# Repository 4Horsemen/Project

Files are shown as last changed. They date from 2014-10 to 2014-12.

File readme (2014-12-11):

----------12/01/14 - 12/07/14 T17 Weekly Update 7-----------
*Thomas and Brian soldered all components onto their PCBs
*Thomas and Brian verified their PCBs had no solder bridges
*Fabricated bamboo parts for our Useless Box
*Worked on finalizing code for the Useless Box
*Designed arm mechanism for our Useless Box

----------11/24/14 - 11/30/14 T17 Weekly Update 6-----------
*Turned in HW#6
*Finished purchasing all components for PCB
*Thomas and Brian got cleared to work in the EPL & use
 the laser cutter, reflow oven, and soldering stations

----------11/17/14 - 11/23/14 T17 Weekly Update 5-----------
*Assembled our first board and baked it in the oven
*Started on HW#6
*Finalized the design for our test plan and test cases for HW#6

-----------11/10/14 - 11/16/14 T17 Weekly Update 4----------
Completed Tasks:
*Received our PCBs from Osh Park Manufacturing
*Began HW#5
*Researched HW#5
*Completed HW#5 Version #1
*Completed HW#5 Revision #2

-----------11/03/14 - 11/09/14 T17 Weekly Update 3-----------
Completed Tasks:
*Eliminated all unnecessary components in our PCB design
*Finalized our PCB design
*Submitted our PCB design inside the allotted time window
*Began HW#4
*Revised and expanded HW#4
*Completed HW#4
*Began to program Arduino and motor microcontrollers
*Ordered final parts

-----------10/27/14 - 11/02/14 T17 Weekly Update 2------------
Completed tasks:
*Got all of our ICs for our projects ordered
*Designed our schematic
*Fixed communication issues
*Finalized our black box
*Turned in HW#3 Rev#3
*Collective mentality shift.

-----------10/23/14 - 10/24/14 T17 Weekly Update 1------------
Completed tasks:
*Create a weekly update template
*Completed Rev1 HW 3
*Rough draft of Black box design completed

*Updated Block Diagram

To be done next week:
*Start ordering parts
*finish Atmega328 research
*finish LED Array research
*finish Servo research

Issues:
*Not sure what circuitry would be needed for LED arrays
*Not sure of motor/servo control circutry
*Getting Patrick, Ahmad, and Thomas on to git
*Getting the Atmega to respond to our preferences

---------------------------------------------------

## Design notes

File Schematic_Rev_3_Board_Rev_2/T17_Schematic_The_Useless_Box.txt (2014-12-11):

Partlist exported from C:/Users/Brian/Documents/GitHub/tut/Schematic_Rev_3_Board_Rev_2/T17_Schematic_The_Useless_Box.sch at 12/11/2014 2:39:47 PM

Part            Value                 Device                Package            Description                                 PROD_ID    TP_SIGNAL_NAME VALUE     
9V-BATTERY-CLIP M02LOCK               M02LOCK               1X02_LOCK          Standard 2-pin 0.1" header. Use with                                            
C1              10uF                  C-EUC0805             C0805              CAPACITOR, European symbol                                                      
C2              10uF                  C-EUC0805             C0805              CAPACITOR, European symbol                                                      
C3              10nF                  C-EUC0805             C0805              CAPACITOR, European symbol                                                      
C4              10nF                  C-EUC0805             C0805              CAPACITOR, European symbol                                                      
C5              10nF                  C-EUC0805             C0805              CAPACITOR, European symbol                                                      
C6              10uF                  C-EUC0805             C0805              CAPACITOR, European symbol                                                      
C7              10uF                  C-EUC0805             C0805              CAPACITOR, European symbol                                                      
C8              10nF                  C-EUC0805             C0805              CAPACITOR, European symbol                                                      
C9              10nF                  C-EUC0805             C0805              CAPACITOR, European symbol                                                      
C10             22pF                  C-EUC0805             C0805              CAPACITOR, European symbol                                                      
C11             22pF                  C-EUC0805             C0805              CAPACITOR, European symbol                                                      
C12             10nF                  C-EUC0805             C0805              CAPACITOR, European symbol                                                      
IC1                                   V_REG_78XX-TO-220     TO-220-ALT         Voltage Regulator                                                               
J1              AVR_SPI_PRG_6NS       AVR_SPI_PRG_6NS       2X3-NS             AVR ISP 6 Pin                                                                   
JP3             ARM_SERVO             M03PTH                1X03               Header 3                                                                        
JP4             LID_SERVO             M03PTH                1X03               Header 3                                                                        
L-MOTOR         M02LOCK               M02LOCK               1X02_LOCK          Standard 2-pin 0.1" header. Use with                                            
PROGRAMMING                           M06NO_SILK_FEMALE_PTH 1X06_NO_SILK       Header 6                                    CONN-08437                          
Q1              16MHz                 XTAL/S                QS                 CRYSTAL                                                                         
R-MOTOR         M02LOCK               M02LOCK               1X02_LOCK          Standard 2-pin 0.1" header. Use with                                            
R1              0                     R-EU_R0805            R0805              RESISTOR, European symbol                                                       
R2              10K                   R-EU_R0805            R0805              RESISTOR, European symbol                                                       
R3              10K                   R-EU_R0805            R0805              RESISTOR, European symbol                                                       
R4              10K                   R-EU_R0805            R0805              RESISTOR, European symbol                                                       
R5              10K                   R-EU_R0805            R0805              RESISTOR, European symbol                                                       
R6              10K                   R-EU_R0805            R0805              RESISTOR, European symbol                                                       
S1              SWITCH-MOMENTARY-2SMD SWITCH-MOMENTARY-2SMD TACTILE-SWITCH-SMD Various NO switches- pushbuttons, reed, etc SWCH-08247                          
TOGGLE          M02LOCK               M02LOCK               1X02_LOCK          Standard 2-pin 0.1" header. Use with                                            
U$1             LB1938FA-AH           LB1938FA-AH           MSOP8                                                                                              
U$2             LB1938FA-AH           LB1938FA-AH           MSOP8                                                                                              
U1              ATMEGA328P            ATMEGA328_SMT         TQFP32-08          32-Pin Atmega328 part                       IC-09069                  ATMEGA328P

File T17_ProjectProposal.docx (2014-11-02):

HW #2: Project Proposal

Useless Box!!

The design is a simplistic 3.5"x4.5"x3.5" box with a switch on the lid.

Must

- Have a box
- Have a switch
- Have a servo
- Have a battery

Can

- Have a second, hidden, switch for power turning the lid switch into a signal
- Have Motors and hidden wheels to create an interactive experience
- Have a second servo to make movements more distinct (one lifts lid, second flips switch)
- Have a Gyroscope to sense direction and speed for greater control on interaction.
- Have a proximity sensor to stay on the table

May

- Add LED/LCD/OLED display programmed to express emotion

The box itself will listen for or be powered by a switch on the lid, which will cause a compartment on the lid to lift, and allow a servo controlled "finger" to be revealed and flip the switch back to the original position for an indefinite number of times. The project can have it's difficulty scaled up from there to include extra sensors, servos, and motors for a more complex movement and interaction experienced by the operator. It also may have peripherals such as LED displays to create a character out of the box and give it emotion.

ECE 411 Fall 2014 practicum project wiki Authors: Patrick L., Ahmad Q., Thomas S. Brian A.

| difficulty | programming difficulty | circuitry | Mechanical difficulty | research | Scalability | cost | | scale
rudder pedals | 6 | 7.5 | 6 | 7 | 3 | 1 | 5 | | 1. so simple a child can do it
transformer soft start | 8 | 3 | 8 | 5 | 10 | 3 | 10 | | 5. Easily doable by a EE Jr.
transcranial mag ther | 10 | 10 | 10 | 6 | 10 | 10 | 10 | | 10. Research level engineering
mobile charge det. | 7 | 5 | 8 | 5 | 6 | 1 | 5
slot cars | 7.5 | 3 | 8 | 8 | 4 | 1 | 7
useless box | 5 | 3 | 3 | 6.5 | 3 | 1 | 4
critera priority: (rated highest to lowest) | 7 | 3 | 2 | 1 | 4 | 6 | 5

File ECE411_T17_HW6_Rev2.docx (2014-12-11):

Ahmad Qazi

Brian Andrews (T17)

Patrick Liggett

Thomas Scarpinatto

November 24, 2014

# ECE411 HW # 6: Test Plan Rev 2

## Comprehensive Hierarchical Test Plan

THE USELESS BOX: System Test Plan

1. INTRODUCTION
  1.1 This Document
  1.2 Conduct System Tests
2. REFERENCE DOCUMENTS
  2.1 Design Documentation

• TBU Requirements Document, Rev 3

• TBU Project Schedule, Rev 2

• TBU System Design/Modeling, Rev 2

• TBU Block Level Diagram, Rev 3

• TBU Power Supply Schematic, Rev 2

• TBU Comprehensive Schematic, Rev 3.5

• TBU Board Layout, Rev 3

  2.2 Other

• Atmel ATMega328 Design Specifications

• Atmel ATMega328 8-Bit Microcontroller Datasheet

• ON Semiconductor LB1938FA Motor Driver Datasheet

3. TBU Overview
  3.1 Operational Description
  3.2 Definition of Terminology
4. PRETEST PREPARATION
  4.1 Test Equipment

• Tektronix Multimeter DMM4020

4.2 Test Setup and Calibration

5. The Switch
  5.1 Verify Switch is Active High
  5.2 Verify Switch is the only input
  5.3 Switch fires high every time it is thrown on
6. ATMega328
  6.1 Verify signal input each time switch is toggled to high position
  6.2 Verify that servos get signal each time the switch is toggled
  6.3 Verify that Motor Control Chip (MCC) gets sent a signal every eighth time the switch is toggled
7. Motor Control Chip (MCC)
  7.1 Verify that MCC receives signal every eighth time the switch is toggled
  7.2 Verify sequence of forward and reverse on wheel motors
8. Power Supply
  8.1 Verify 5V output
  8.2 Verify input and output current within supply specifications

## Test Case # 1: The Toggle Switch

Test Writers: Ahmad Qazi, Brian Andrews, Patrick Liggett, Thomas Scarpinatto
Test Case Name: | | The Useless Box Test #1 | | | | Test ID #: | | TUB-01
Description: | | Verify that the toggle switch is the only input signal for the whole system. | | | | Type: | | Black box

Tester Information
| Name of Tester: | | | | | | Date:
Hardware Ver: | | 1.0 | | | | | Time:
Setup: | | Make sure the Switch is in off position and the battery is viable.
Step | Action | Expected Result | Pass | Fail | N/A | | Comments
1 | Plug lead into test point between switch and ATMega328 | Test lead should fit into point
2 | Verify zero signal before engaging switch | Meter should read zero signal
3 | Flip switch to on position | Meter should read 5V
4 | Record data gathered | Meter readings should be within design parameters
Overall Test Result:

## Test Case # 2: ATMega328

Test Writers: Ahmad Qazi, Brian Andrews, Patrick Liggett, Thomas Scarpinatto
Test Case Name: | | The Useless Box Test #2 | | | | Test ID #: | | TUB-02
Description: | | | | | | Type: | | Black box

Tester Information
| Name of Tester: | | | | | | Date:
Hardware Ver: | | 1.0 | | | | | Time:
Setup: | | Plug leads in test points between switch and ATMega328, between ATMega328 and Arm Servo, between ATMega328 and Lid Servo and between ATMega328 and Motor Control Chip.
Step | Action | Expected Result | Pass | Fail | N/A | | Comments
1 | Plug lead into test point between switch and ATMega328 | Signal should be zero when switch is low and 5V when switch is high.
2 | Plug lead into test point between ATMega328 and Arm Servo | Signal through Arm servo should be zero when switch is low and 5V when switch is high.
3 | Plug lead into test point between ATMega328 and Lid Servo | Signal through Lid servo should be zero when switch is low and 5V when switch is high.
4 | Plug lead into test point between ATMega328 and Motor Control Chip | Signal through MCC should be zero when switch is low and 5V when switch is high.
Overall Test Result:

## Test Case # 3: Motor Control Chip

Test Writers: Ahmad Qazi, Brian Andrews, Patrick Liggett, Thomas Scarpinatto
Test Case Name: | | The Useless Box Test #3 | | | | Test ID #: | | TUB-03
Description: | | Check if Motor Control Chip (MCC) activates when triggered and functions correctly | | | | Type: | | Black box

Tester Information
| Name of Tester: | | | | | | Date:
Hardware Ver: | | 1.0 | | | | | Time:
Setup: | | Make proper connections to the MCC daughterboard via ATMega328 or Arduino.
Step | Action | Expected Result | Pass | Fail | N/A | | Comments
1 | Toggle switch every 8th time to verify that MCC activates | TBU moves due to activation.
2 | Truth table (TT) verification by using given truth table | Truth table outputs match given TT.
Overall Test Result:

## Test Case # 4: Power Supply

Test Writers: Ahmad Qazi, Brian Andrews, Patrick Liggett, Thomas Scarpinatto
Test Case Name: | | The Useless Box Test #4 | | | | Test ID #: | | TUB-04
Description: | | System should run on a 9V battery but converts to 5V during the process | | | | Type: | | Black box

Tester Information
| Name of Tester: | | | | | | Date:
Hardware Ver: | | 1.0 | | | | | Time:
Setup: | | Connect 9V battery to IC
Step | Action | Expected Result | Pass | Fail | N/A | | Comments
1 | Verify output voltage is 5V | Output is found to be 5V
2 | Measure I/O current and check if it is within supply specifications | I/O current is found to be ≤ 1.5 A
Overall Test Result:

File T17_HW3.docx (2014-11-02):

ECE411: Industry Design Processes: HW # 3

Brian Andrews, Ahmad Qazi, Patrick Liggett, Thomas Scarpinatto

Oct 27, 2014

REV 3

Must

• Have a box

• Have a switch

• Have a servo

• Have a battery

Can

• Have a second, hidden, switch for power turning the lid switch into a signal

• Have Motors and hidden wheels to create an interactive experience

• Have a second servo to make movements more distinct (one lifts lid, second flips switch)

• Have a Gyroscope to sense direction and speed for greater control on interaction.

• Have a proximity sensor to stay on the table

May

• Add LED/LCD/OLED display programmed to express emotion

Marketing Requirements | Engineering Requirements | Justification
2-4 | 1. System should run on a 9V Battery | Increases the runtime of the device, and keeps the device portable.
2, 3 | 2. The box dimensions should not exceed 6”x5”x3” | The small size keeps the product portable. This means it can be used as a small entertainment device such as a "Newton's cradle" or "infinite slinky"
1, 2 | 3. Microcontroller should have a minimum of 1 PWM. Should have a minimum of 10 programmable I/O lines. Maximum of 9V. Minimum of 512 bytes of internal SRAM. Should be operated at milspec temperatures. | Ensures that the useless box can operate at room temperature, low power, and still run the necessary components.
1, 2 | 4. Should have one motorized arm, one moveable door, and two switches. | The low number of actuators and inputs reduces the overall cost and complexity of the design.
2 | 5. Production cost should not exceed $40. | This is based on competitive market and the non-commercialized nature of the device.

Marketing Requirements

1. The system should be robust enough to withstand being dropped repeatedly as well as being water resistant. The switches must not break and be able to withstand constant use.
2. The system should be low cost for ease of Marketing.
3. The system should be portable. The device should be able to fit into a backpack pocket or briefcase compartment.

4. The system should be easy to use. The device will have at most two

switches.

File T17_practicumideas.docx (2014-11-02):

Ahmad Qazi

Brian Andrews

Patrick Liggett

Thomas Scarpinatto

Oct 13, 2014

ECE411: INDUSTRY DESIGN PROCESSES: PROJECT PROPOSAL

1) Rudder Pedals (for Simulator Use)- All planes have a flap on the tail that is used to help the plane turn left or right based upon the flap’s position. These are controlled by a pair of pedals in the cockpit that upon depressing the corresponding left or right pedal shifts the rudder into position for turning left/right. Many video games that involve plane flight simulate this rudder as a part of the game’s mechanics. While usually these are pre-programmed to react perfectly due to the limited number of inputs a player has access to.

Many people who play games that involve plane flight prefer to use a H.O.T.A.S. (Hands On Throttle And Stick) setup in order to have a more intimate and realistic experience. The downside of this setup is that you no longer have access to keyboard shortcuts that allow control of the plane’s rudder. Many of these H.O.T.A.S. setups solve this by making the flight stick have a rotational axis for rudder control, Some companies even offer highly priced pedal sets to appease the gamers who prefer a more realistic experience. The proposal is to design a microcontroller based system that could be easily self assembled and turned into rudder pedals that can be used in these simulation games.

2) Transformer Soft Start – When a transformer is first powered up, it can grab as much as forty times its rated operating current, causing very serious heat rise in the laminations of the core. Each time this happens, the lifespan of the transformer is reduced. In times past, this has been a very minor issue, but grid power becomes more and more distributed, especially with intermittent power supplies from renewable sources such as wind turbines and photovoltaics, transformers are being switched on and off more and more, thereby greatly increasing wear and tear and shortening the lifespan of the transformer.

Given that the purchase lead-time on a utility scale transformer is around three years, the need to maximize transformer lifetime is paramount. Additionally, many of the locations for renewable sources of power such as wind turbines and wave power generation sites are in very out-of-the-way locales that have no back-up transformers that can be paralleled in to maintain a continuous flow of power. What this translates to is that potentially hundreds of millions of dollars worth of power generating equipment sits idle while the transformer is either repaired in field or removed and replaced.

What we propose is a soft starting mechanism similar to that used by large DC motors, especially ones with large physical loads present on startup. A bank of resistors would be placed in-line for the start up of the transformer with a resistor being removed each time the transformer reaches a predetermined level of power so that the startup is much more gradual and thereby does not superheat the laminations inside the transformer core. Our device would monitor the flux increase inside the core and pull out resistors as the transformer meets predefined criteria, thereby increasing life expectancy and decreasing maintenance costs.

3) Transcranial Magnetic Therapy Device (TCrMT) – Transcranial Magnetic Therapy (TCrMT) has been a boon for bipolar, schizophrenic, and head trauma patients, but so far has been used mostly in a laboratory context. This valued treatment is not widely available to patients that desperately need it when it should be available everywhere. Our proposal is to make a small, portable TCrMT device that can be carried around in a backpack and is ready for deployment at a moment’s notice so that the patient does not have to live in fear of having an episode of seizures or a psychotic episode out in the general public. The patient would self-conduct the treatment by placing a special cap on their head and plugging it into the TCrMT device and pressing a single start button.

The length of the treatment would be determined by simple mechanical switches and push buttons that are ruggedized to withstand the inevitability of being dropped and tossed about. Power will come from a lithium-ion polymer battery that can be recharged from 120/240 VAC or 12 VDC power sources. This device would be mostly absent of sophisticated ICs to hold down device cost and to increase reliability and device longevity.

4) Mobile Charge Detection Device – Electricians have very simple detection devices that will tell you if a cable is energized or not, but what we put forward is a mobile device that detects not just power, but what type. Specifically, this device would be able to discern the difference between AC and DC power sources, and if the power detected is AC, then the components of real and reactive power would be displayed in their respective proportions on an easy to view lighted screen. Such a device would be very useful for diagnosis in large IC fabrication units and laboratory settings so that the safety and integrity of hypersensitive test equipment, some devices costing millions of dollars, is assured. We would also like the device, if it is so possible to achieve, to be able to see power conduits through sheet rock so that electricians and handymen do not injure themselves by accidentally striking hot power lines that they cannot see.

5) Slot Cars!! - The proposal here is to design a track and car base system. The tracks should be usable like a puzzle piece allowing players to design their own track as long as it contains the keystone track that has the controllers attached. This can be as simple as an oval for demonstration purposes. As for the cars, if we can design a base that allows tops to be clipped on we could make it so that the bodies of the cars themselves can be 3-D printable.

6) Useless Box!! - A box with a switch on top, as simple a design as could be. What happens when we flip the switch? A lid lifts away from the rest of the box and out pops a little finger shaped object that rotates up and flips the switch back. This can scale up in difficulty or down very easily, with extra time we can add to the software and hardware making the box react differently (back away from it’s original position, drive around, spin in place, make faces on LED arrays etc.)

According to the Decision Matrix attached

1. Useless Box
2. Mobile Charge Detection Device
3. Rudder Pedals
4. Slot Cars

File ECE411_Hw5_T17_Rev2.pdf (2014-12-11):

# ECE411: INDUSTRY DESIGN PROCESSES

# HOMEWORK 5

# REV 2

## BRIAN ANDREWS

## THOMAS SCARPINATTO

## AHMAD QAZI

## PATRICK LIGGETT

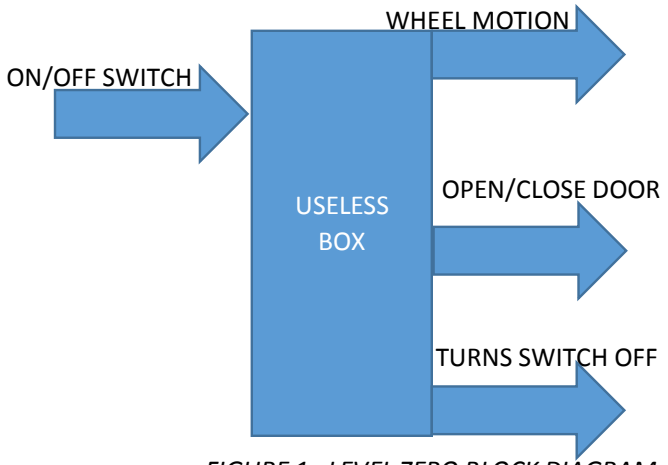
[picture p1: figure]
WHEEL MOTION; ON/OFF SWITCH; OPEN/CLOSE DOOR; TURNS SWITCH OFF; USELESS BOX

FIGURE 1: LEVEL ZERO BLOCK DIAGRAM

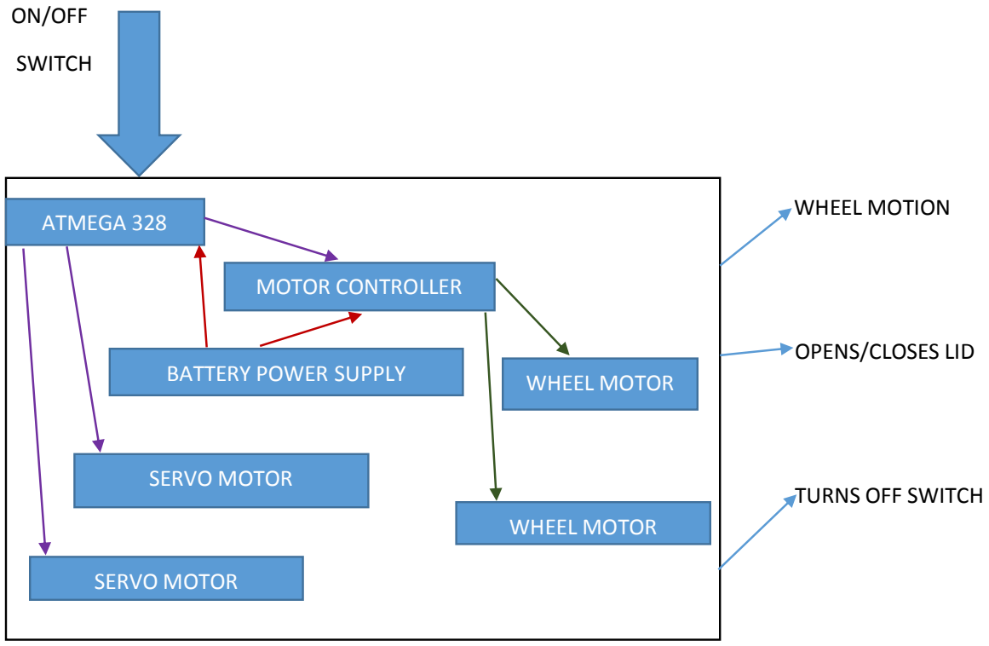
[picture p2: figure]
ON/OFF; SWITCH; WHEEL MOTION; OPENS/CLOSES LID; TURNS OFF SWITCH; ATMEGA 328; MOTOR CONTROLLER; BATTERY POWER SUPPLY; WHEEL MOTOR; SERVO MOTOR

FIGURE 2: LEVEL ONE BLOCK DIAGRAM

## LEVEL-0 DIAGRAM FOR EACH SUB-COMPONENT

SWITCH | ATMega328

User Input

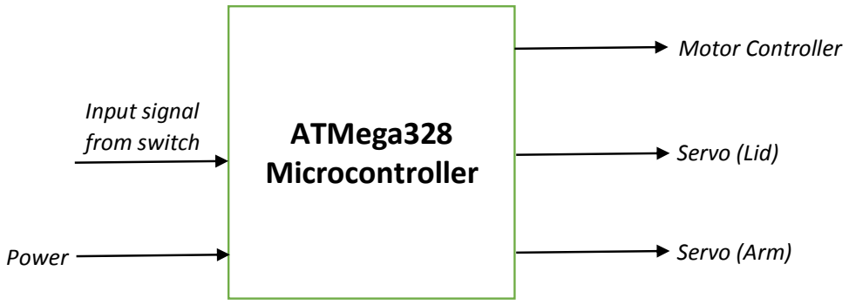
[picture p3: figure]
ATMega328 Microcontroller; Motor Controller; Servo (Lid); Servo (Arm); Input signal from switch; Power

### Motor Controller

# 1

Wheel Motor #1 ATMega328

Power

### Motor Controller

# 2

Wheel Motor #2 ATMega328

Power

Lid Servo | Lid ATMega328

Power

Arm Servo | Arm

Power

ATMega328

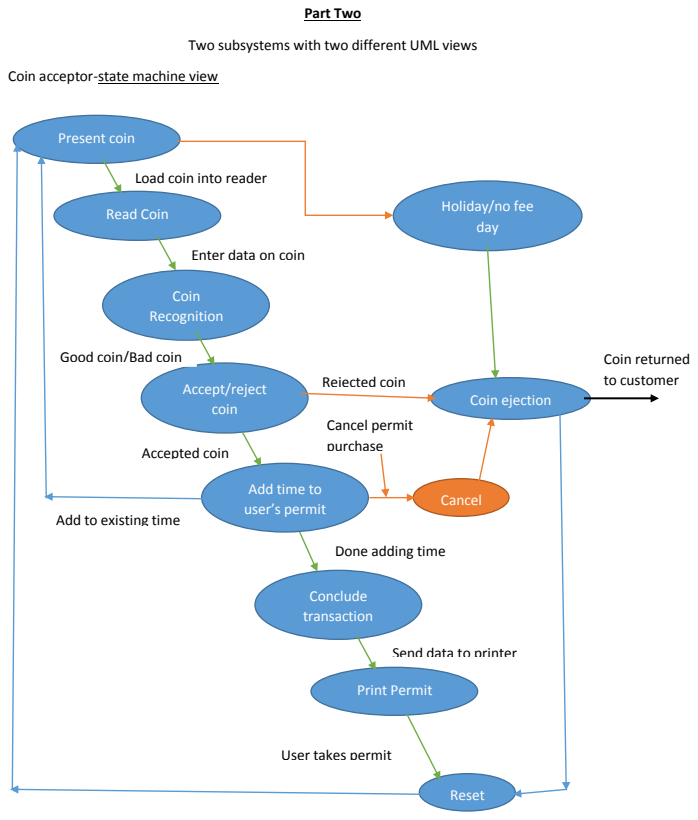
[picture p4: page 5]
Part Two; Present coin; Read Coin; Coin Recognition; Accept/reject coin; Conclude transaction; Print Permit; Reset; Cancel; Coin ejection; Rejected coin; Accepted coin; Cancel permit purchase; Coin returned to customer

Two subsystems with two different UML views

Coin acceptor-state machine view

Load coin into reader

Holiday/no fee
day

Enter data on coin

Good coin/Bad coin

Add time to
user’s permit

Add to existing time

Done adding time

Send data to printer

User takes permit

## THE COIN ACCEPTOR – PHYSICAL VIEW

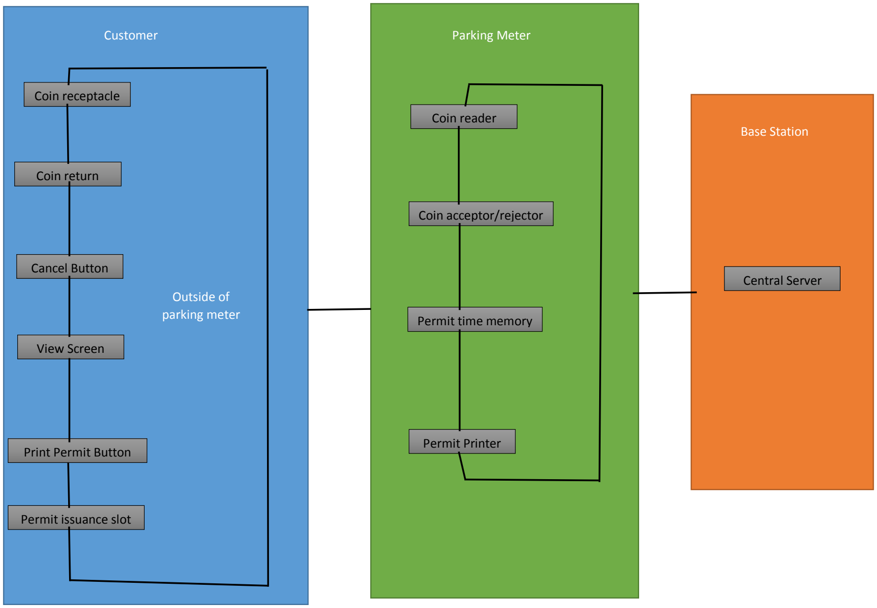
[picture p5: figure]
Customer; Coin receptacle; Coin return; Cancel Button; View Screen; Print Permit Button; Permit issuance slot; Outside of parking meter; Parking Meter; Coin reader; Coin acceptor/rejector; Permit time memory; Permit Printer; Base Station; Central Server

## THE CREDIT CARD READER – THE STATE MACHINE VIEW

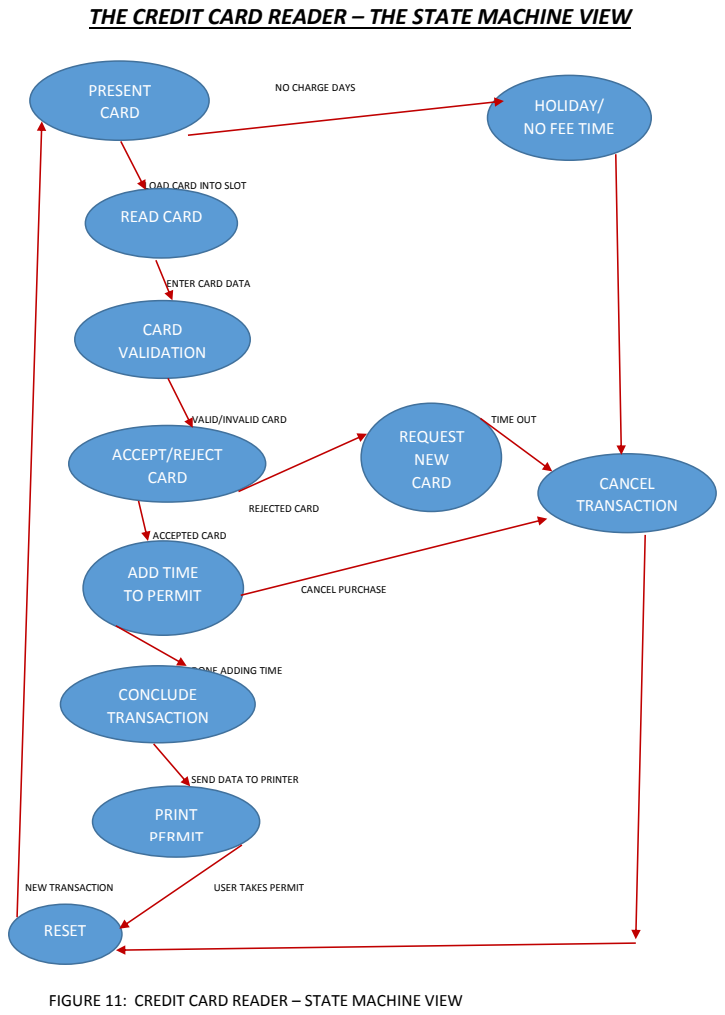
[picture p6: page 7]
VALID/INVALID CARD; TIME OUT; REJECTED CARD; ACCEPTED CARD; CANCEL PURCHASE; NEW TRANSACTION; USER TAKES PERMIT; PRESENT CARD; CARD VALIDATION; ACCEPT/REJECT CARD; ADD TIME TO PERMIT; CONCLUDE TRANSACTION; RESET; REQUEST NEW; CARD; CANCEL; TRANSACTION

NO CHARGE DAYS

HOLIDAY/
NO FEE TIME

LOAD CARD INTO SLOT
READ CARD

ENTER CARD DATA

DONE ADDING TIME

SEND DATA TO PRINTER
PRINT
PERMIT

FIGURE 11: CREDIT CARD READER – STATE MACHINE VIEW

# CREDIT READER – INTERACTION VIEW

Customer | Parking Meter | Base Station | CC Database

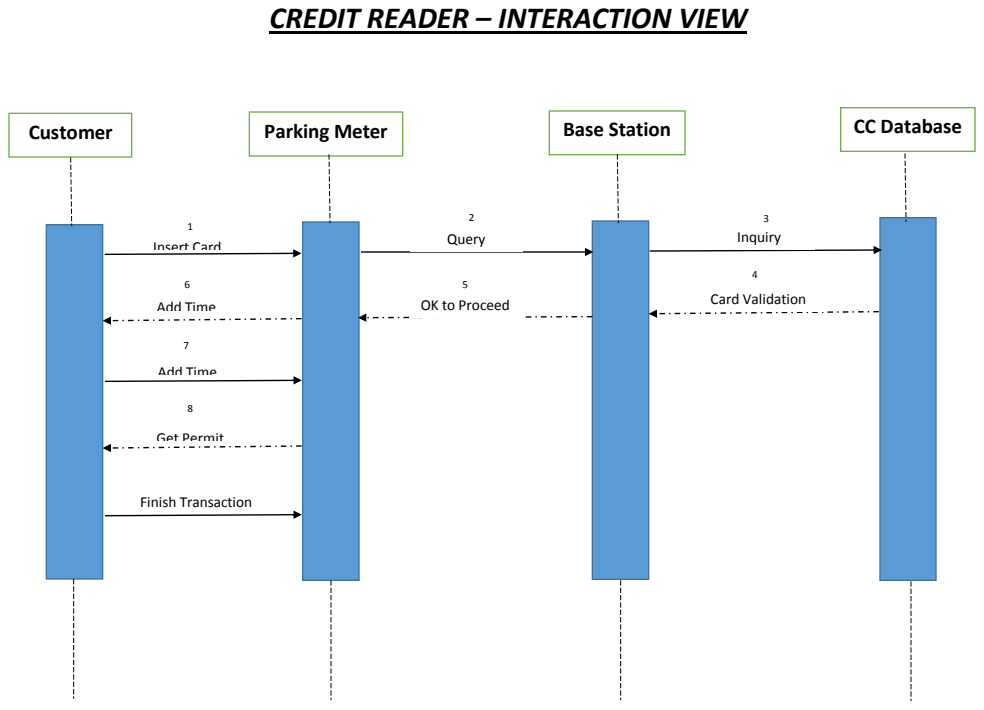
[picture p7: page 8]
Insert Card; Add Time; Get Permit; Finish Transaction; Query; Inquiry; Card Validation

OK to Proceed

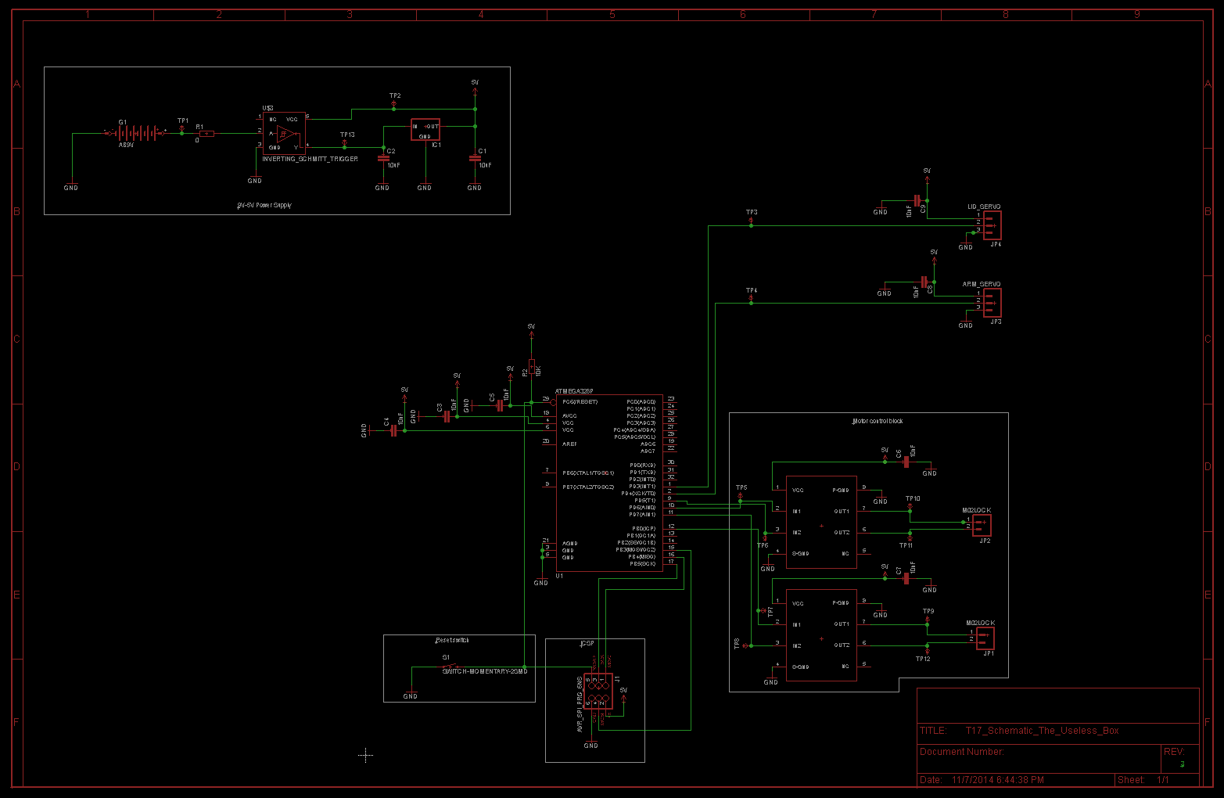
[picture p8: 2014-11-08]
T17_Schematic_Image.PNG

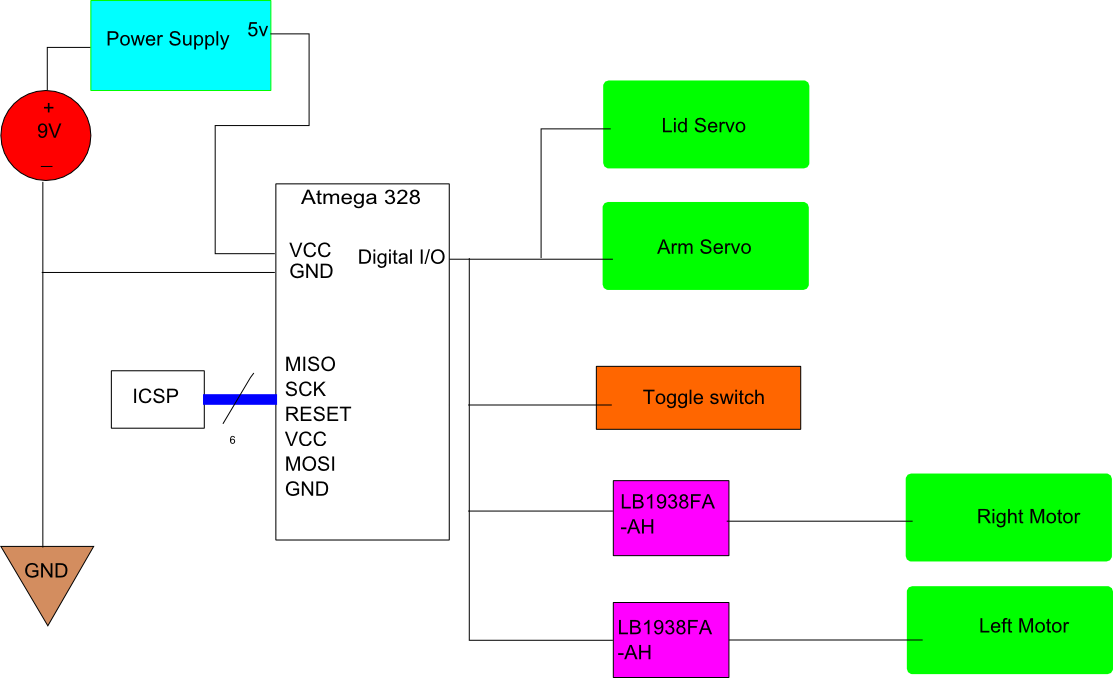
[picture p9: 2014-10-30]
T17_Blackbox.png

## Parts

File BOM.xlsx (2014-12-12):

PART | VALUE | DEVICE | PACKAGE | Description | Product ID | PRICE FOR 1 | PRICE FOR 1000
C1 | 10uF | C-EUC0805 | C0805 | CAPACITOR, European symbol |  | $0.17 | $31.63
C2 | 10uF | C-EUC0806 | C0806 | CAPACITOR, European symbol |  | $0.17 | $31.63
C3 | 10uF | C-EUC0807 | C0807 | CAPACITOR, European symbol |  | $0.17 | $31.63
C4 | 10uF | C-EUC0808 | C0808 | CAPACITOR, European symbol |  | $0.17 | $31.63
C5 | 10uF | C-EUC0809 | C0809 | CAPACITOR, European symbol |  | $0.17 | $31.63
C6 | 10uF | C-EUC0810 | C0810 | CAPACITOR, European symbol |  | $0.17 | $31.63
C7 | 10uF | C-EUC0811 | C0811 | CAPACITOR, European symbol |  | $0.17 | $31.63
C8 | 10uF | C-EUC0812 | C0812 | CAPACITOR, European symbol |  | $0.17 | $31.63
C9 | 10uF | C-EUC0813 | C0813 | CAPACITOR, European symbol |  | $0.17 | $31.63
C10 | 22pF | C-EUC0814 | C0814 | CAPACITOR, European symbol |  | $0.10 | $15.60
C11 | 22pF | C-EUC0815 | C0815 | CAPACITOR, European symbol |  | $0.10 | $15.60
C12 | 10nF | C-EUC0816 | C0816 | CAPACITOR, European symbol |  | $0.36 | $86.95
IC1 |  | V_REG_78XX-TO-220 | TO-220-ALT | Voltage Regulator |  | $4.30 | $3604.32
 |  |  |  | 40 pin header row |  | $0.56 | $282.15
JP3 | ARM_SERVO | M03PTH | 1X03 | Header 3 |  | $8.95 | $7160.00
JP4 | LID_SERVO | M03PTH | 1X03 | Header 3 |  | $8.95 | $7160.00
LMOTOR | M02LOCK | M02LOCK | 1X02_LOCK | Standard 2-pin 0.1" header. Use with |  | $0.50 | $500.00
RMOTOR | M02LOCK | M02LOCK | 1X02_LOCK | Standard 2-pin 0.1" header. Use with |  | $0.50 | $500.00
Q1 | 16MHz | XTAL/S | QS | CRYSTAL |  | $0.36 | $1.92
R1 | 0
R2 | 10K | R-EU_R0805 | R0805 | RESISTOR, European symbol |  | $0.10 | $7.04
R3 | 10K | R-EU_R0806 | R0806 | RESISTOR, European symbol |  | $0.10 | $7.04
R4 | 10K | R-EU_R0807 | R0807 | RESISTOR, European symbol |  | $0.10 | $7.04
R5 | 10K | R-EU_R0808 | R0808 | RESISTOR, European symbol |  | $0.10 | $7.04
R6 | 10K | R-EU_R0809 | R0809 | RESISTOR, European symbol |  | $0.10 | $7.04
S1 | SWITCH-MOMENTARY-2SMD | SWITCH-MOMENTARY-2SMD | TACTILE-SWITCH-SMD | Various NO switches- pushbuttons, reed, etc SWCH-08247
IC2 | LB1938FA-AH | LB1938FA-AH | MSOP8 |  |  | $1.63 | $759.90
IC3 | LB1938FA-AH | LB1938FA-AH | MSOP8 |  |  | $1.63 | $759.90
MICROPROCESSOR |  | ATMEGA 328P | 32TQFP | 32-Pin Atmega328 part |  | $7.40 | $3790.53
BATTERY CLIP | M02LOCK | M02LOCK | Standard 2-pin 0.1" header. Use with |  | IC-09069
TOGGLE |  |  |  |  |  | $4.32 | $2520.00
 |  |  |  |  | TOTAL | $41.69 | $27,476.74

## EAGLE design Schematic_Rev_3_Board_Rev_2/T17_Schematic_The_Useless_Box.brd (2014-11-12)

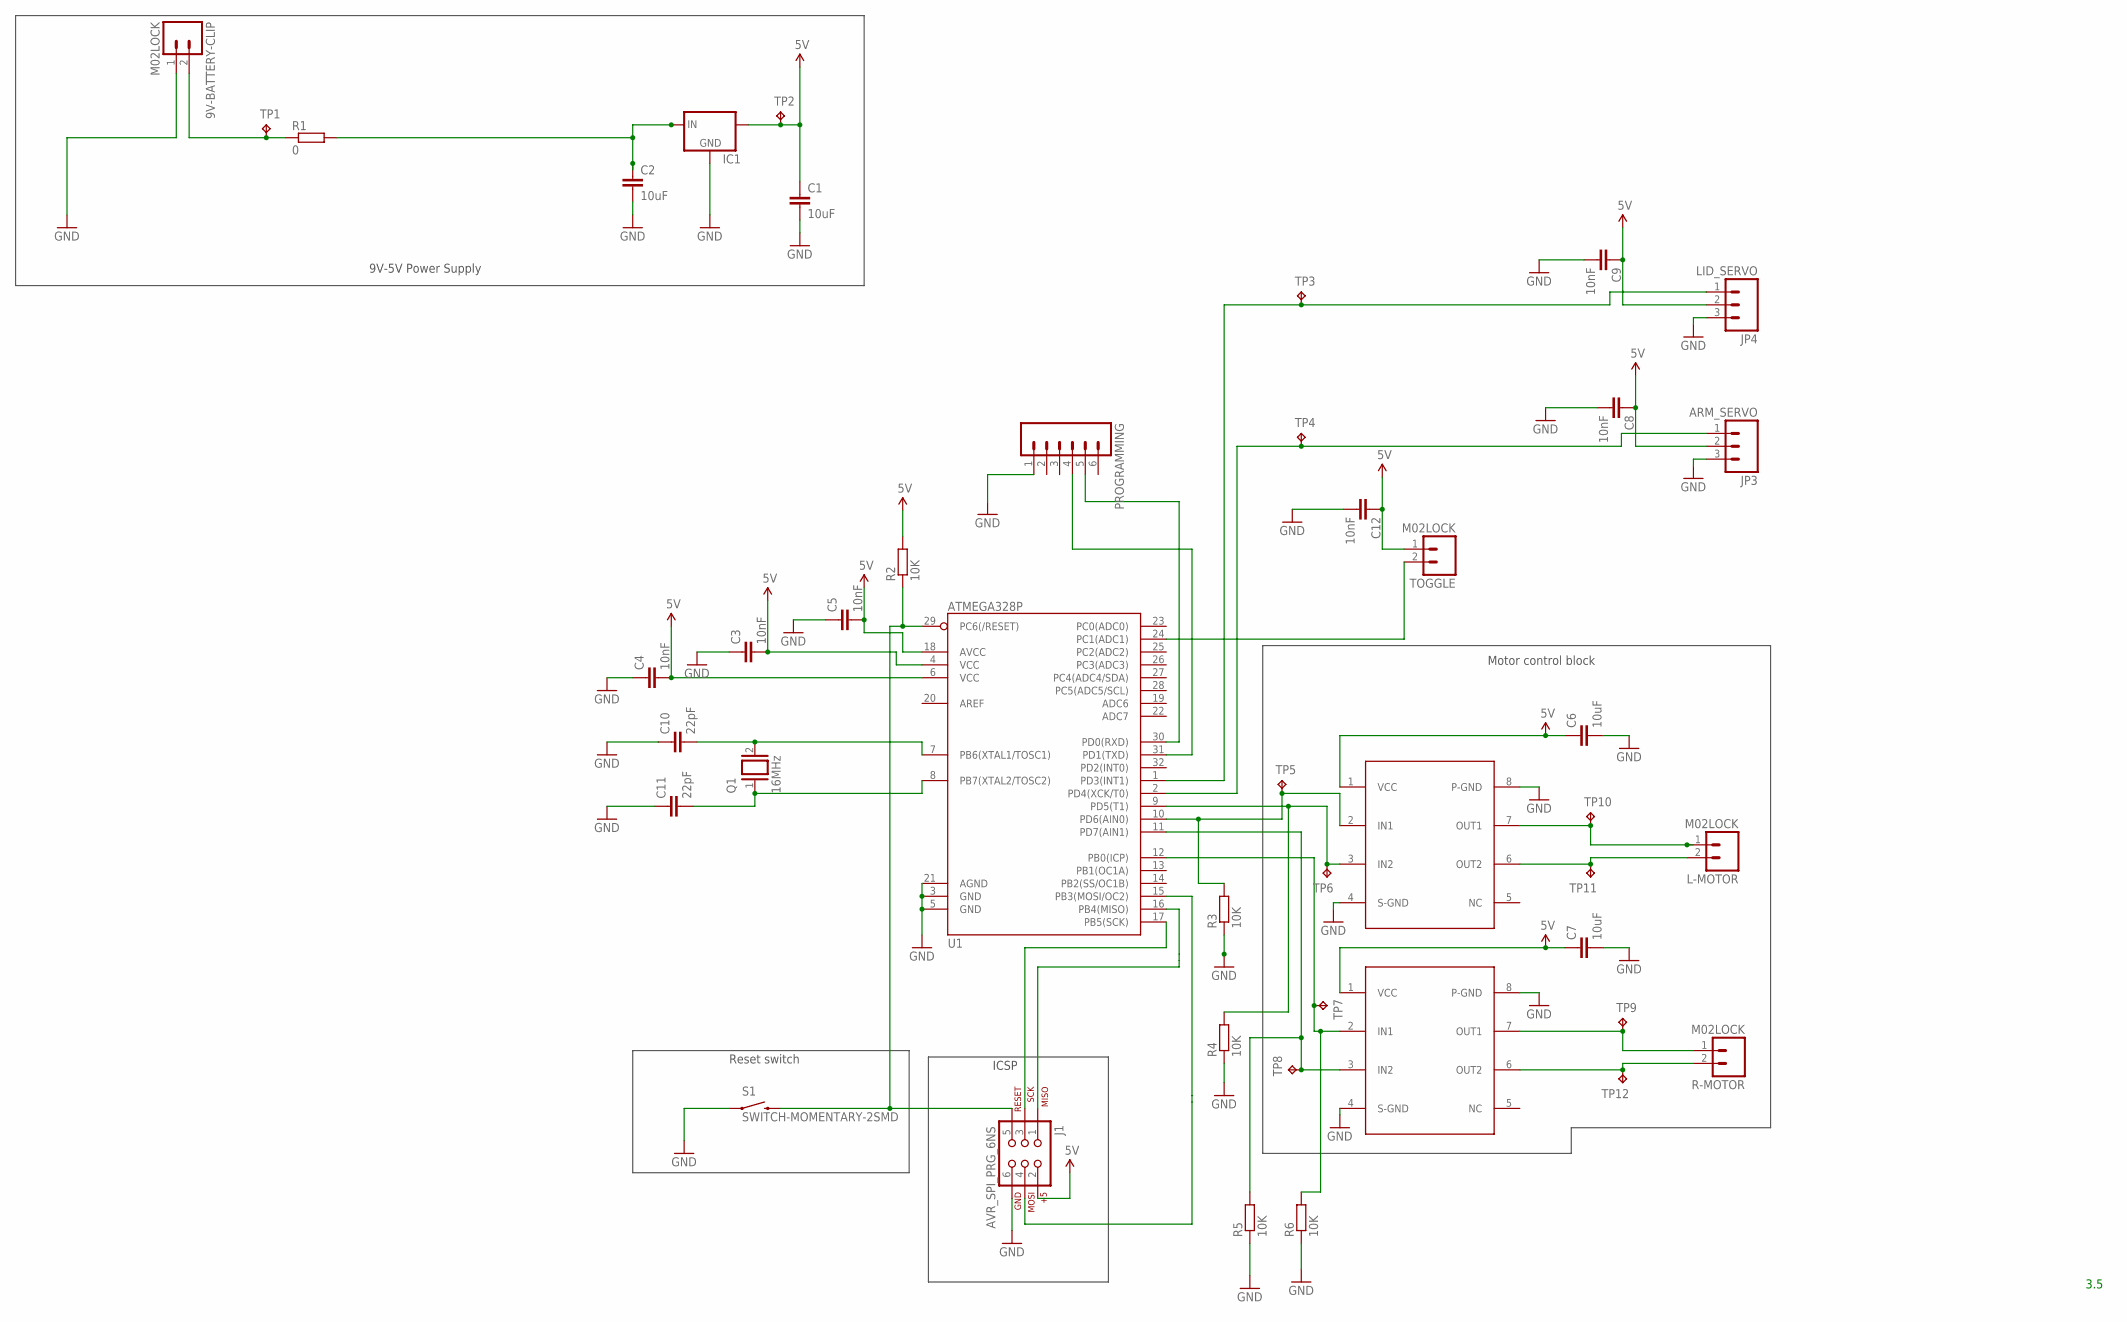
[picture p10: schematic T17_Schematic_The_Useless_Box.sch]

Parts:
9V-BATTERY-CLIP: M02LOCK; 1X02_LOCK
C1, C2, C6, C7: 10uF; C0805
C3, C4, C5, C8, C9, C12: 10nF; C0805
C10, C11: 22pF; C0805
IC1: V_REG_78XX-TO-220; TO-220-ALT
J1: AVR_SPI_PRG_6NS; 2X3-NS
JP3: ARM_SERVO; 1X03
JP4: LID_SERVO; 1X03
L-MOTOR: M02LOCK; 1X02_LOCK
PROGRAMMING: M06NO_SILK_FEMALE_PTH; 1X06_NO_SILK
Q1: 16MHz; QS
R1: 0; R0805
R2, R3, R4, R5, R6: 10K; R0805
R-MOTOR: M02LOCK; 1X02_LOCK
S1: SWITCH-MOMENTARY-2SMD; TACTILE-SWITCH-SMD
TOGGLE: M02LOCK; 1X02_LOCK
TP1, TP2, TP3, TP4, TP5, TP6, TP7, TP8, TP9, TP10, TP11, TP12: TPB1,27; B1,27
U1: ATMEGA328P; TQFP32-08
U$1, U$2: LB1938FA-AH; MSOP8

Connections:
5V: C1.1, C3.2, C4.2, C5.2, C6.1, C7.1, C8.1, C9.1, C12.1, IC1.OUT, J1.2, JP3.2, JP4.2, R2.2, TOGGLE.1, TP2.TP, U1.4 (VCC), U1.6 (VCC), U1.18 (AVCC), U$1.1 (VCC), U$2.1 (VCC)
GND: 9V-BATTERY-CLIP.1, C1.2, C2.2, C3.1, C4.1, C5.1, C6.2, C7.2, C8.2, C9.2, C10.1, C11.1, C12.2, IC1.GND, J1.6, JP3.3, JP4.3, PROGRAMMING.1, R3.1, R4.1, R5.1, R6.1, S1.1, U1.3 (GND), U1.5 (GND), U1.21 (AGND), U$1.4 (S-GND), U$1.8 (P-GND), U$2.4 (S-GND), U$2.8 (P-GND)
unnamed: R6.2, TP7.TP, U1.12 (PB0(ICP)), U$1.2 (IN1)
unnamed: R-MOTOR.1, TP9.TP, U$1.7 (OUT1)
unnamed: R-MOTOR.2, TP12.TP, U$1.6 (OUT2)
unnamed: L-MOTOR.2, TP11.TP, U$2.6 (OUT2)
unnamed: L-MOTOR.1, TP10.TP, U$2.7 (OUT1)
unnamed: R5.2, TP8.TP, U1.11 (PD7(AIN1)), U$1.3 (IN2)
unnamed: J1.4, U1.15 (PB3(MOSI/OC2))
unnamed: JP3.1, TP4.TP, U1.2 (PD4(XCK/T0))
unnamed: PROGRAMMING.5, U1.30 (PD0(RXD))
unnamed: JP4.1, TP3.TP, U1.1 (PD3(INT1))
unnamed: C2.1, IC1.IN, R1.2
unnamed: 9V-BATTERY-CLIP.2, R1.1, TP1.TP
unnamed: R3.2, TP5.TP, U1.10 (PD6(AIN0)), U$2.2 (IN1)
unnamed: J1.3, U1.17 (PB5(SCK))
unnamed: PROGRAMMING.4, U1.31 (PD1(TXD))
unnamed: J1.5, R2.1, S1.3 (2), U1.29 (PC6(/RESET))
unnamed: C11.2, Q1.1, U1.8 (PB7(XTAL2/TOSC2))
unnamed: J1.1, U1.16 (PB4(MISO))
unnamed: C10.2, Q1.2, U1.7 (PB6(XTAL1/TOSC1))
unnamed: R4.2, TP6.TP, U1.9 (PD5(T1)), U$2.3 (IN2)
unnamed: TOGGLE.2, U1.24 (PC1(ADC1))

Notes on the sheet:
3.5
Motor control block
ICSP
Reset switch
9V-5V Power Supply

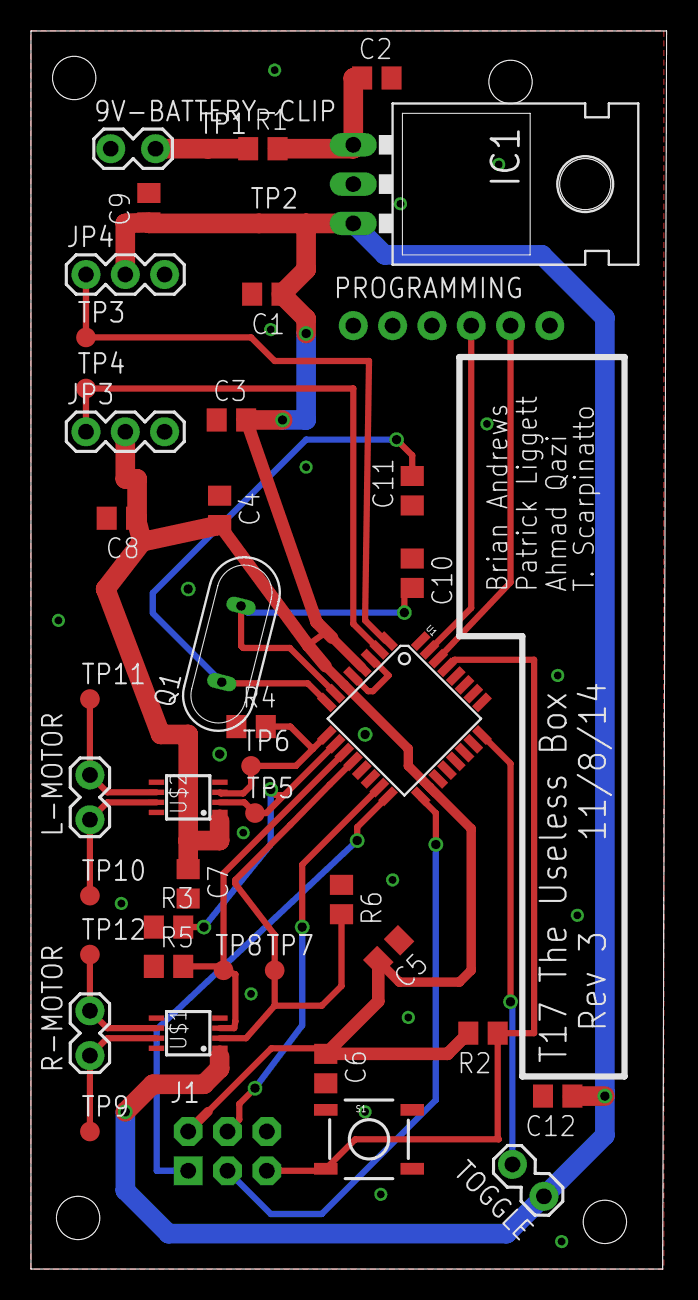
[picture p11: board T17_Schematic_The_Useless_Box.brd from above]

Board: 2 copper layers, 41.1 x 80.0 mm, 44 parts (0 on the bottom side), 23 nets.

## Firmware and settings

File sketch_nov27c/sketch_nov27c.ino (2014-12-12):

#include <Servo.h>  // servo library
Servo servoL;  // lid servo control object
Servo servoA; //arm servo

const int motor1Pinin1 = 6; //first motor controller input 1
const int motor1Pinin2 = 5; //first motor controller input 2
const int motor2Pinin1 = 8; //2nd motor controller input 1
const int motor2Pinin2 = 7; //2nd motor controller input 2

//initializes counter to counter number of times switch toggles to high
int count = 0; 
void setup()
{
  // Set up the switch pin to be an input:
  pinMode(A1, INPUT);

  pinMode(motor1Pinin1, OUTPUT); //sets up motor controllers
  pinMode(motor1Pinin2, OUTPUT);  
  pinMode(motor2Pinin1, OUTPUT);  
  pinMode(motor2Pinin2, OUTPUT);  
  servoL.attach(3); //attach lid and arm servos to pins
  servoA.attach(4);
  Serial.begin(57600); //begin at correct baud rate
}

  void loop()
{
 
  int toggle = 0;  // variables to hold the switch states

//set all motor controllers to low to ready for standby
  digitalWrite(motor1Pinin1, LOW); 
  digitalWrite(motor1Pinin2, LOW); 
  digitalWrite(motor2Pinin1, LOW); 
  digitalWrite(motor2Pinin2, LOW);

  servoL.write(70); //set lid servo to 70 degrees
  servoA.write(20); //set arm servo to 20 degrees
  
  //press toggle switch up to this much, box turns itself off
 while (count < 4) 
  {
    toggle = digitalRead(A1);
    if (toggle == HIGH)
    {
     servoL.write(35); //lid opens first
     delay(1500); //wait for it...
     servoA.write(170); //arm pops out and hits switch back
     delay(1000); //give it time to go back in
     servoA.write(20); //arm goes back in
     delay(2000); //keep lid open for theatrics
     servoL.write(70); //close lid
     delay(1000);
     count++; //keep track of # of times switched
     delay(1000); 
  }
}
//after a certain amount of switches, box gets mad
 if (count >= 4)
  {
    //values needed to turn on motor controllers to "spin" box
    digitalWrite(motor1Pinin1, HIGH); 
    digitalWrite(motor1Pinin2, LOW);
    digitalWrite(motor2Pinin1, LOW);
    digitalWrite(motor2Pinin2, HIGH);
    delay(5000); //give it time to be mad
    digitalWrite(motor1Pinin1, LOW); //turn off motors
    digitalWrite(motor1Pinin2, LOW); 
    digitalWrite(motor2Pinin1, LOW); 
    digitalWrite(motor2Pinin2, LOW); 
   count = 0; //reset to start all over again
  } 
}

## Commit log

2014-10-30 adding schematic
    [T17_Schematic_The_Useless_Box.sch]
2014-10-30 adding photo of schematic for reference
2014-11-04 Added Latest Version of the schematic and the board
    [T17_Schematic_The_Useless_Box.brd, T17_Schematic_The_Useless_Box.sch]
2014-11-05 Circuit rev...? board rev 1
    [T17_Schematic_The_Useless_Box.brd, T17_Schematic_The_Useless_Box.sch]
2014-11-05 Circuit revision checked, this is rev 2. modified the circuit schematic to reflect as much in the bottom right. Stay tuned for Rev 3.
    [T17_Schematic_The_Useless_Box.sch]
2014-11-08 Added Rev 3 circuit, board rev 2
    [T17_Schematic_The_Useless_Box.brd, T17_Schematic_The_Useless_Box.sch]
2014-11-08 ACTUALLY updating the schematics this time. Picture added for modification on the wiki.
    [T17_Schematic_The_Useless_Box.brd, T17_Schematic_The_Useless_Box.sch]
2014-11-09 Added mounting holes and ground plane staples
    [T17_Schematic_The_Useless_Box.brd, T17_Schematic_The_Useless_Box.sch]
2014-11-10 submittable board?
    [T17_Schematic_The_Useless_Box.brd, T17_Schematic_The_Useless_Box.sch]
2014-11-12 Adding the final ckt design
    [T17_Schematic_The_Useless_Box.brd, T17_Schematic_The_Useless_Box.sch]
2014-12-11 adding BOM rev 1, box's box, and code rev 1
2014-12-12 adding commented code and bill of materials rev 2
    [BOM.xlsx]

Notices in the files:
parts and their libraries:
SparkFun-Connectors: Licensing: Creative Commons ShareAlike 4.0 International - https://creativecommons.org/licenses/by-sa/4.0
